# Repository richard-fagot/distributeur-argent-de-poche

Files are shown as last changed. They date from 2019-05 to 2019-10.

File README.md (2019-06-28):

# Distributeur automatique d'argent de poche pour les enfants.

Pour qu'ils puissent faire "comme les grands", avoir une carte bleue personnalisée et saisir un code pour pouvoir retirer leur argent de poche au distributeur, mais uniquement le samedi.

L'objectif est de faire un truc fun pour les enfants (et pour moi aussi du coup :D). Et comme tout ne va pas se dérouler sans accros, j'en profite pour tenir un journal de bord des problèmes rencontrés et des solutions trouvées pour les résoudre.

Tant qu'à y être, ça me semble intéressant de partager tout ça, alors ce journal de bord sert de base à une présentation sous forme de quickie plein de trucs et astuces dans chacun des domaines du projet.

# Disciplines associées

- **La programmation Arduino**, pour coder la logique du distributeur :
    - C++,
    - Optimisation de la taille du code généré,
    - Minimisation de la fragmentation du tas,
    - Gestion du temps ;

- **L'électronique**, pour l'alimentation, les différents composants autour de l'arduino, la fabrication du PCB, la lecture de carte à puce... :
  - Design du schéma életronique,
  - Routing,
  - Gravure du PCB,
  - Soudage ;

- **La conception 3D** pour dessiner les pièces mécaniques, supports et boitier du distributeur :
    - Conception des pièces,
    - Définition des liaisons mécaniques,
    - Assemblage des différents éléments entre eux ;

- **L'impression 3D**, pour fabriquer les pièces conçues sur mesure :
    - Slicing,
    - Prise en compte des contraintes liées au FDM ;

# Matériel
- Arduino Nano ;
- Pavé numérique à matrice (keypad) ;
- Écran LCD 2004 (4 lignes de 20 caractères) avec module I2C ;
- Module RTC DS3231 (ne pas prendre le DS1307 car il dérive beaucoup (il peut perdre plus d'une minute par jour)) en I2C ;
- 2 micro servos type HXT900 ;
- Connecteur carte à puce ;
- Lot de carte à puce vierge SLE4442.

# Logiciel
- [**Arduino IDE**](https://www.arduino.cc/en/Main/Software) ou VSCode avec l'extension Arduino ;
- [**Fusion 360**](https://www.autodesk.com/products/fusion-360) pour modéliser les pièces mécaniques ;
- [**Cura**](https://ultimaker.com/en/products/ultimaker-cura-software) pour préparer les pièces destinées à l'impression 3D ;
- [**Tinkercad**](https://www.tinkercad.com) pour la simulation d'un environnement Arduino ;
- [**EasyEDA**](https://easyeda.com) pour la conception de la partie électronique et du routage du PCB.

# Références
- Éviter la fragmentation de la pile : https://cpp4arduino.com/2018/11/06/what-is-heap-fragmentation.html 
- SLE4442 sur hackaday: https://hackaday.com/2008/11/25/how-to-read-a-fedex-kinkos-smart-card-sle4442/
- SLE4442 datacheet : http://www.smartcardsupply.com/PDF/DS_sle4432_42_0795.pdf
- SLE4442 sur docplayer : https://docplayer.fr/3533459-Carte-a-puce-sle-4432.html
- SLE4442 Librairie de lecture/écriture pour arduino : https://sourceforge.net/p/arduinosclib/wiki/Home/
- LCD 2004 https://www.gotronic.fr/pj2-sbc-lcd20x4-fr-1440.pdf
- D13 en input et pullup ne marche pas : https://www.developpez.net/forums/d1623869/general-developpement/programmation-systeme/embarque/arduino/propos-led_builtin-arduino-nano/

# Changement de taille programme

Passage de 61% à 57%
1. sans optim 18740
1. string name -> char name[21] 18674
1. dans un case string -> char 18596
1. un sprintf explose la taille 19246
1. remplacé par {'0'+total} 17740
1. sort la condition du if -> 17728

Plus tard
1. Aprés la création de la classe SamrtCard 12620/1046
1. MyKeyPad                                 12700/1070
1. Suppresion des Serial                    11522/821 (ce sont les string à la volée qui occupent la mémoire dynamique)
1. MyTime                                   11522/821

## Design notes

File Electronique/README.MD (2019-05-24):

Schéma électronique créé avec [EasyEDA](https://easyeda.com)

Le fichier DAAP.json est un export direct d'*EasyEDA*.

Les PDF sont les exports imprimables du schéma et du PCB.

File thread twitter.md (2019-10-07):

#

Un petit #THREAD pour détailler un peu plus mon talk au #DevfestToulouse
⬇️⬇️⬇️

#

Ce projet fait intervenir plein de domaines différents : conception 3D, impression 3D, électronique, arduino, C++, fabrication de PCB, un peu de mécanique, etc.

#

La conception 3D a été faite avec #Fusion360 (mais on peut utiliser #sketchup #Blender3d et plein d'autres) parce que c'était nouveau pour moi, il est super intuitif et qu'il y a une grosse communauté autour de ce logiciel pour apprendre facilement à s'en servir.

==> photo du projet fini dans Fusion360

#

Le design a été pensé pour tenir compte des contraintes de l'#impression3D :
- limiter les porte-à-faux ;
- tenir compte du sens d'impression des pièces subissant des contraintes mécaniques ;
- limiter la quantité de matière ;
- Faire des pièces qui s'impriment en 2h à 3h max.

#

J'ai voulu des temps d'impression courts d'une part parce que j'ai régulièrement des coupures de courant chez moi et que mon imprimante n'a pas de fonction "resume" et, d'autre part, parce que ça facilite le prototypage en pouvant plus facilement refaire une pièce défectueuse.

#

Pour la partie électronique j'ai utilisé ces composants :
- écran LCD2004 (20 cols, 4l) ;
- module I2C pour le LCD ;
- module RTC (horloge temps réel) ;
- Arduino nano ;
- Clavier matriciel 4x4 ;
- Servo HXT900 de modélisme ;
- Connecteur de carte à puce ;
- Carte à puce SLE4442.

#

Tous ces composants ont une librairie qu'on trouve facilement dans le gestionnaire de bibliothèque sauf pour la carte à puce. Il faut aller la trouver sur le net : https://sourceforge.net/p/arduinosclib/wiki/Home/
Et se la garder quelque part au cas où le lien disparaisse.

#

D'ailleurs, je vous recommande d'annoter vos imports de librairie dans le code avec suffisamment de détails pour la retrouver. Les librairies pour clavier matriciel ont la fâcheuse tendance à s'appeler "keypad.h".

#

Pour programmer la carte à puce et y mettre le code secret, la somme d'argent à distribuer et le prénom de l'enfant c'est par là : https://github.com/richard-fagot/DAAP-Smartcard

#

Sans rien changer aux branchements du distributeur on peut l'utiliser tel quel pour programmer une carte à puce, le mettre à l'heure et faire la distribution d'argent de poche uniquement en téléversant le programme qui va bien.

#

Pour la carte à puce : https://github.com/richard-fagot/DAAP-Smartcard

Pour l'heure il suffit de prendre les programmes d'exemple du DS3231.

#

L'horloge me permet de contrôler que les enfants ne font pas plus d'un retrait par semaine (samedi ou dimanche) en gérant les changements de mois et les années bissextiles.

#

Je n'en ai pas parlé pendant le talk mais il y a du code #cpp, beaucoup de code, que vous pouvez retrouver là : https://github.com/richard-fagot/distributeur-argent-de-poche/tree/master/sketch

Le point d'entrée c'est Sketch.ino à ouvrir dans l'IDE arduino : https://www.arduino.cc/en/Main/Software

#

Dans ce sketch il y a une première fonction 𝘀𝗲𝘁𝘂𝗽() d'initialisation des paramètres du programme et des périphériques. Le fonction 𝗹𝗼𝗼𝗽() contient la logique du programme. Une bonne pratique consiste à faire en sorte qu'elle s'exécute très rapidement.

#

C'est surtout pour dire qu'il faut remplacer les 𝗱𝗲𝗹𝗮𝘆() qui bloquent l'arduino par :

	𝗶𝗳(𝗺𝗶𝗹𝗹𝗶𝘀() - 𝗽𝗿𝗲𝘃𝗶𝗼𝘂𝘀𝗠𝗶𝗹𝗹𝗶𝘀 > 𝗺𝗼𝗻𝗗𝗲𝗹𝗮𝘆) {...}

ça permet de faire d'autres tâches en attendant qu'un servomoteur ait fini de tourner par exemple.

#

La gestion du temps c'est compliqué ! Sur ce projet j'ai mis en place une machine à état parce que c'est ce qui me semblait le plus naturel pour gérer les différents états du distributeur mais aussi les délais et notamment ceux qui concernent les mouvements des servos.

#

Mais attention aux noeuds au cerveau :D

#

Pour coder on peut utiliser l'IDE Arduino mais on peut aussi utiliser VS Code avec l'extension #Arduino (il sert à tout ce VS Code) et ça marche plutôt bien même si il y a des écarts sur la taille des programmes. Il faudrait regarder du côté des options de compilation du #cpp.

#

À un moment j'ai grillé un servo en faisant une fausse manipulation. J'ai cherché un logiciel qui permettrait de simuler un environnement #arduino et des périphériques autours, comme des servos.

#

Hé bien ça existe ! c'est @tinkercad. J'ai fait une grosse partie de la conception grâce à ça, sans rien casser ! On peut s'en servir comme dans @scratch ou en code pur. Et utiliser des servos, des LCD, la mémoire EEPROM...

#

Quand la phase de prototypage est terminée on va créer le PCB. J'ai utilisé @EasyEDA mais on peut utiliser aussi @kicad_pcb qui est open source.

==> image du pcb

#

Après il suffit de suivre cet excellent tuto de @Heliox_Lab en prenant un papier glacé le plus fin possible pour éviter le gondolage : https://youtu.be/UTe3eYCj6vU

#

Et quand tout est enfin terminé, on profite du résultat final :

(Qu'est-ce que t'en dit @Heliox_Lab ? :D)

Si vous avez des questions, mes DM sont ouverts.

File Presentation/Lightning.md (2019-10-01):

---
pagetitle: DAAP
lang: fr-FR
compile: pandoc -t revealjs -V theme=white -s Lightning.md -o lightning.html --css=devfest.css 
---

# Distributeur Automatique d'Argent de Poche

Richard Fagot

:::notes

1. Tiens-toi bien ;
1. Pense à ta première phrase ;
1. Prend une inspiration ;
1. Embrasse la salle d'un regard et lance-toi.

==> Bonjour à tous et bienvenu. Il y a quelques temps avec mon épouse...
:::

# {data-background-image="assets/img/calvin.png" data-background-size="contain"}
<!--![](assets/img/calvin.png)-->

::: notes
Passer rapidement.

==> Mais on ne s'est pas lancé comme ça...
:::

# 
:::notes
On trouve des règles qu'on a choisi d'appliquer. 

- règles de l'argent de poche :
  - quantité libre,
  - distribution 1x/sem,
  - Pas de privation,
  - not(rémunération),
  - l'enfant dépense librement.

==> L'idée étant qu'ils puissent faire comme les grands...
:::

# {data-background-image="assets/img/comme-les-grands.jpg"}

::: notes

==> quitte à faire comme les grands, est-ce qu'on ne pourrait pas aller plus loin ?

:::

# {data-background-image="assets/img/fond-mouvement.png"}
<!-- image du servomoteur {data-background-color="#FDFAFE"}-->
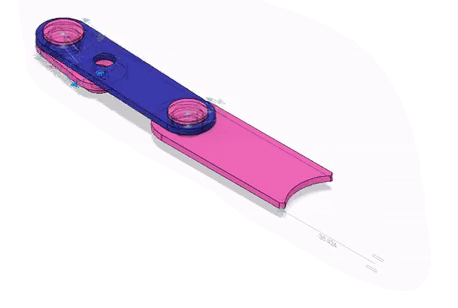
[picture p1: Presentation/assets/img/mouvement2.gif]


:::notes

Passez rapidement pour ne pas perdre l'attention de l'auditoire.

Transforme mvt de rotation en translation alternatif

==> Il y a une colonne de pièce, on pousse celle du dessous...
:::

# 
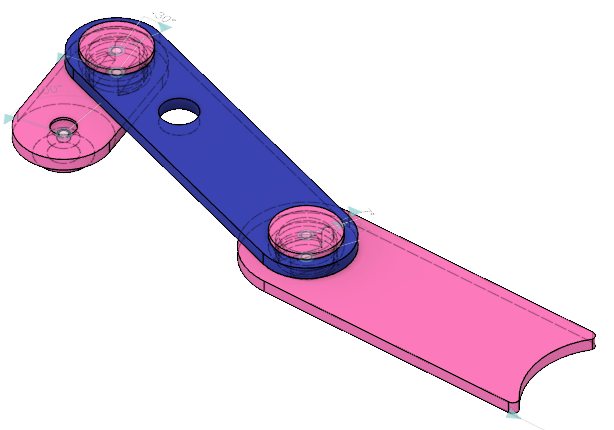
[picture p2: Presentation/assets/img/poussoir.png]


::: notes
  - sujet en soi ;
  - explication des différentes pièces ;
  - penser à la méthode de production.

  ==> vous pourrez venir me voi à l'office hour pour savoir pourquoi il y a un trou dans la bielle.
:::

# {data-background-image="assets/img/impressionPosition.png"}
<!--
![](assets/img/Impression clip.png){ width=1000px }
-->
:::notes
  => pour maintenir tout ça en place il faut un support.
:::

# 
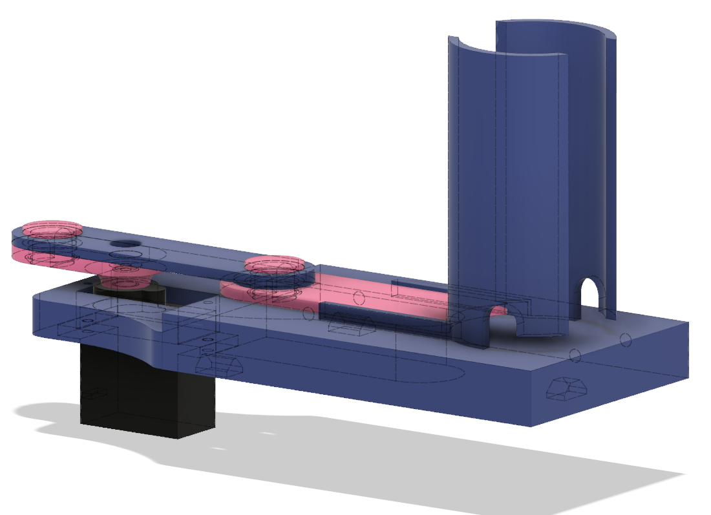
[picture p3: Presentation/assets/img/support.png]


::: notes
  => on peut distribuer, oui, mais combien ? il faut stocker la somme quelque part.
:::

# 
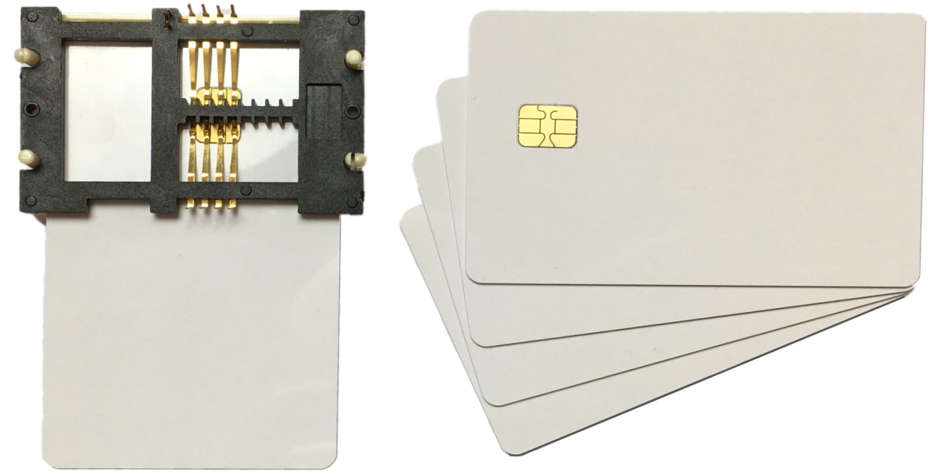
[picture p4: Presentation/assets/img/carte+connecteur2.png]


:::notes
  ne pas parler de la secu.
  - ~~carte sécurisée~~ ;
  - connecteur ;
  - on y stocke : code, prénom et somme.

  => il faut interagir avec l'utilisateur.
:::

# 
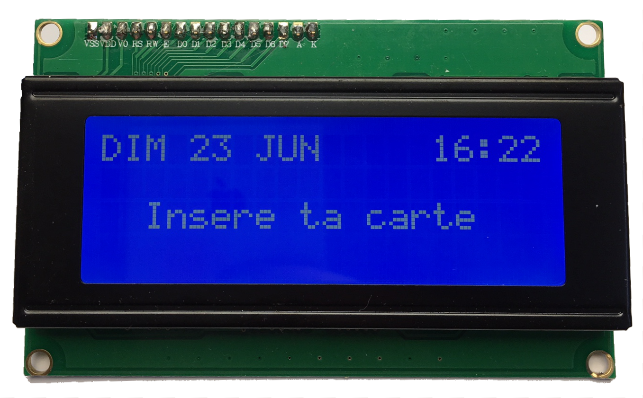
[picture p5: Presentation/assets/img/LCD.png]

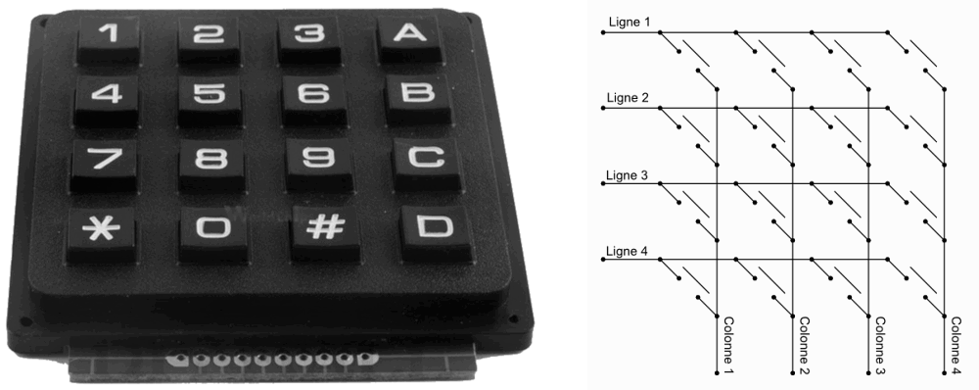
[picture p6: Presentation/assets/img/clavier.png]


::: notes
  ==> Il faut contrôler tout ça.
:::

# 
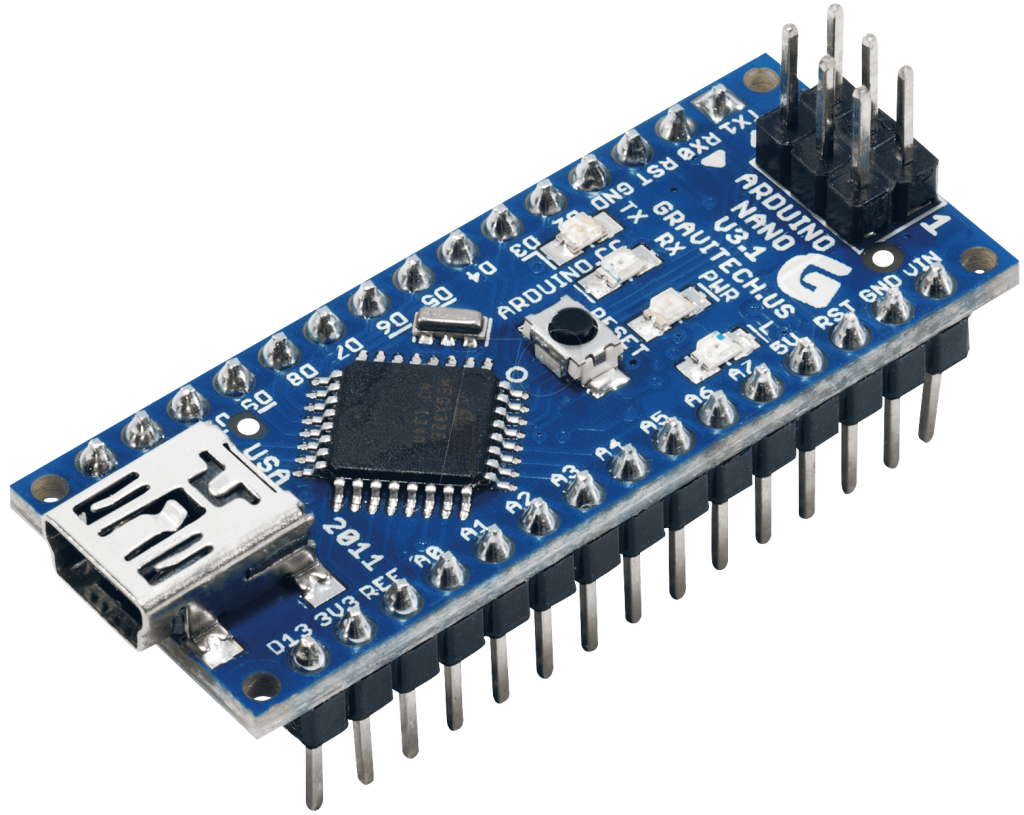
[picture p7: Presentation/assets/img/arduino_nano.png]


:::notes
  - peu de broches => I2C ;
  - Retour aux bases de l'info : pointeurs, références, gestion de la mémoire (fragmentation).

  ==> Tous ces éléments il faut les connecter pendant le prototypage.
:::

# {data-background-image="assets/img/prototype.jpg"}
<!--![](assets/img/prototype.jpg){ height=1080px }
![](assets/img/breadboard.jpg){ height=600px }-->

::: notes

  ==> Ce n'est pas utilisable pour le produit final, il faut un PCB.
:::

# {data-background-image="assets/img/circuit.png" data-background-size="90%"}
<!--![](assets/img/circuit.png){ height=650px }-->

::: notes
  - fait avec EasyEDA ;
  - Pas de fils de connection, mais des étiquettes qui permettent de tout ordonner par fonction.

  ==> Cette description logique permet de passer au routage.
:::

# {data-background-image="assets/img/routing_Bleu.png" data-background-size="60%"}
<!--![](assets/img/routing_Bleu.png){ height=700px }-->
<!--![](assets/img/PCB2.png){ height=600px }-->

::: notes
  - automatique ne marche pas trop ;
  - on fait des aller-retour avec le schéma électronique pour affiner le routage.

  ==> ensuite on imprime et après un peu de chimie et avoir piqué le gemey-maybelline de ma chère moitié.
:::

# {data-background-image="assets/img/dissolvant.jpg" data-background-size="50%"}
<!--![](assets/img/dissolvant.jpg){height="700px"}-->

::: notes
comment ne pas perturber avec le solvant.

  ==> c'est bien le flacon rose qu'il faut, on obtient ça.
:::

# {data-background-image="assets/img/PCB étamé.jpg" data-background-size="60%"}
<!--![](assets/img/PCB étamé.jpg){ width=800px }-->

::: notes
  ==> après perçage et soudage on obtient un résultat bien plus propre que le tas de nouille.
:::

# {data-background-image="assets/img/circuit-monté.jpg" data-background-size="100%"}
<!--![](assets/img/Circuit imprimé.jpg){ width=700px }-->

::: notes
  ==> Tout ça c'est beau mais il faudrait un beau boitier pour ranger le tout.
  ==> Et après de nombreux tests.
:::

# {data-background-image="assets/img/tests.png"}

# 
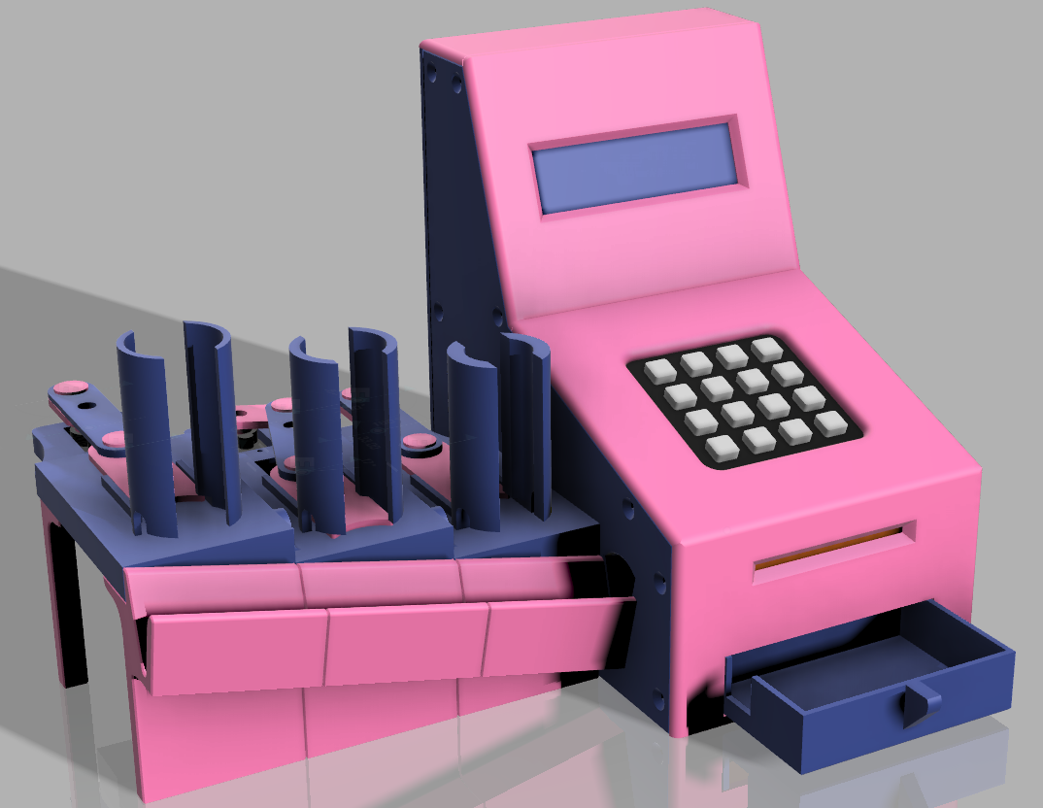
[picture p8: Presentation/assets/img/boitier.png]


# 
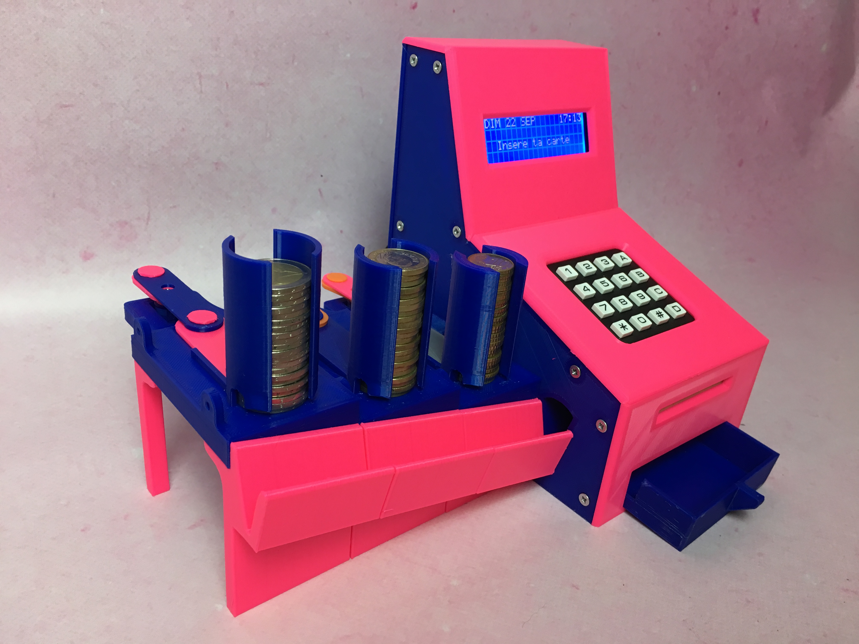
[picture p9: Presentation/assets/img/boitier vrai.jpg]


# Démo


# 

* 2 mois de travail++ ;
* Mécanique, Conception/Impression 3D, Électronique, Arduino, PCB, soudure... ;

# Office Hour

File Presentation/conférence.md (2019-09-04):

---
pagetitle: DAAP Conf
lang: fr-FR
---

<!-- Phrase d'introduction -->
# Distributeur Automatique d'Argent de Poche

Richard Fagot

:::notes
1. Tiens-toi bien ;
1. Pense à ta première phrase ;
1. Prend une inspiration ;
1. Embrasse la salle d'un regard et lance-toi.
:::

<!-- Pause blagounette -->
# 
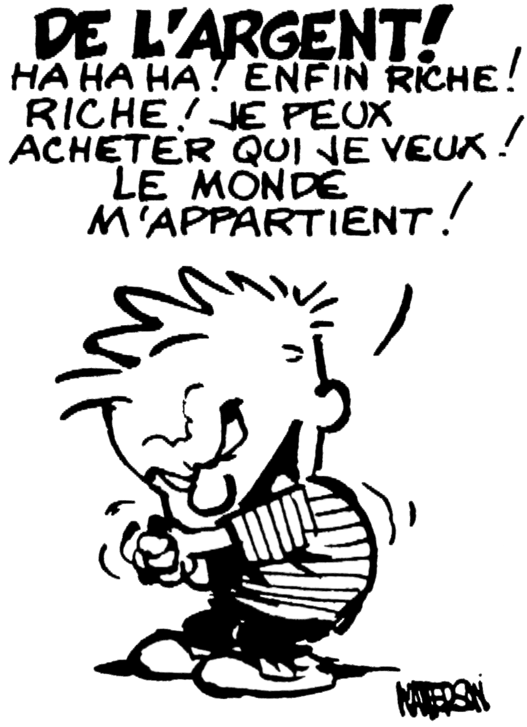
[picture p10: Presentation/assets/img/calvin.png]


::: notes
Passer rapidement.

==> littérature sur le sujet
:::

<!-- Courte introduction à l'argent de poche et genèse du projet -->
#

:::notes
- règles de l'argent de poche (qté libre, 1x/sem, Chq sem, not(rémunération), libre).

==> quitte à faire comme les grands, est-ce qu'on peu aller plus loin ?
:::

<!-- Le poussoir -->
# 


::: notes
**Le poussoir**

- mouvement bielle-manivelle ;
- rotation -> translation.

==> parce que j'aime bien le mouvement
:::

#
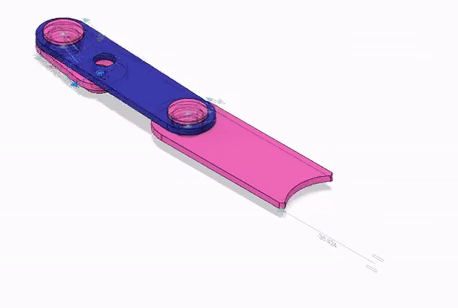
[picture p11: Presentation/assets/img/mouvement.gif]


:::notes
Passez rapidement pour ne pas perdre l'attention de l'auditoire.

- joli ;
- hypnotique ;
- facile à concevoir.

==> il est constitué de != éléments
:::

# 


:::notes
**Le poussoir**

- description + servo ;
- conception dans fusion360 ;
- axes qui maintiennent les pièces ensembles lego.

==> essai paramètre fexibilité, jeu, je suis arrivé à ça.
:::

<!-- Clip -->
#
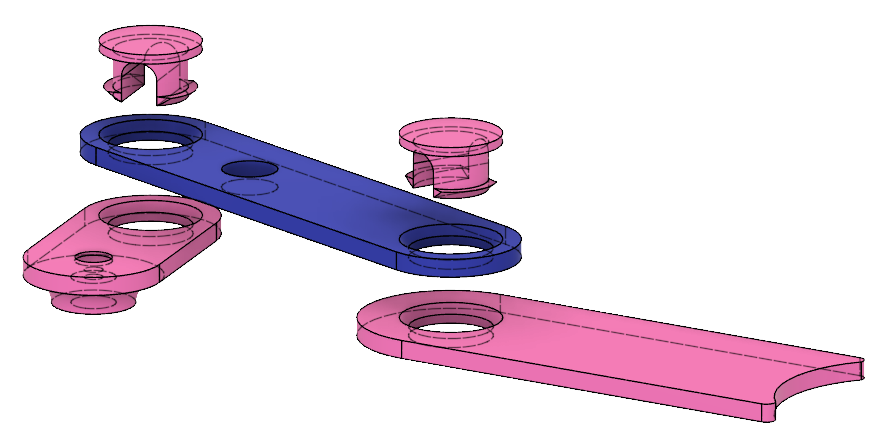
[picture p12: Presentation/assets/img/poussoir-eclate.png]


:::notes
- Description du clip ;
- Pièce complexe : penser à l'impression 3D
:::

#
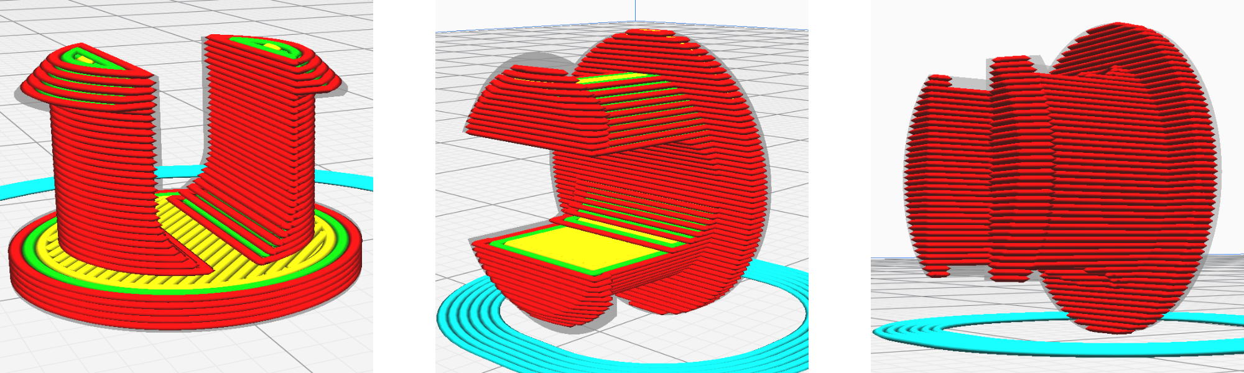
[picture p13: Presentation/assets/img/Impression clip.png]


:::notes
  - paramètres d'impression dans Cura (Simplify3D) ;
  - Pros'n Cons des 3 impressions ;
  - insertion manivelle/poussoir ;
  - mouvement rectiligne, support servo, réservoir pièce.

  ==> Je vous présente le support.
:::

<!-- Le support -->
#
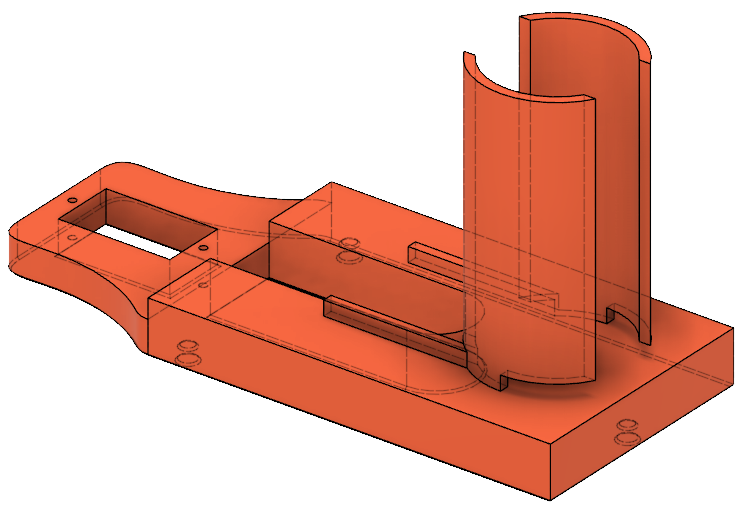
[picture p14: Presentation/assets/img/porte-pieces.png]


::: notes
  - support servo ;
  - guide poussoir ;
  - Diamètre réservoir
  - ouverture réservoir ;
  - rainure réservoir.
git
  ==> système complet, y' plus qu'à le commander
:::

<!-- Arduino -->
#


:::notes
  - Facile à programmer, communauté ;
  - compact ;
  - HE14 à un rang ;
  - nombre de broches ;
  - µC quesako ?

==> Code librairie **OU** chaque carte a son schéma d'entrée-sortie
  
:::

##
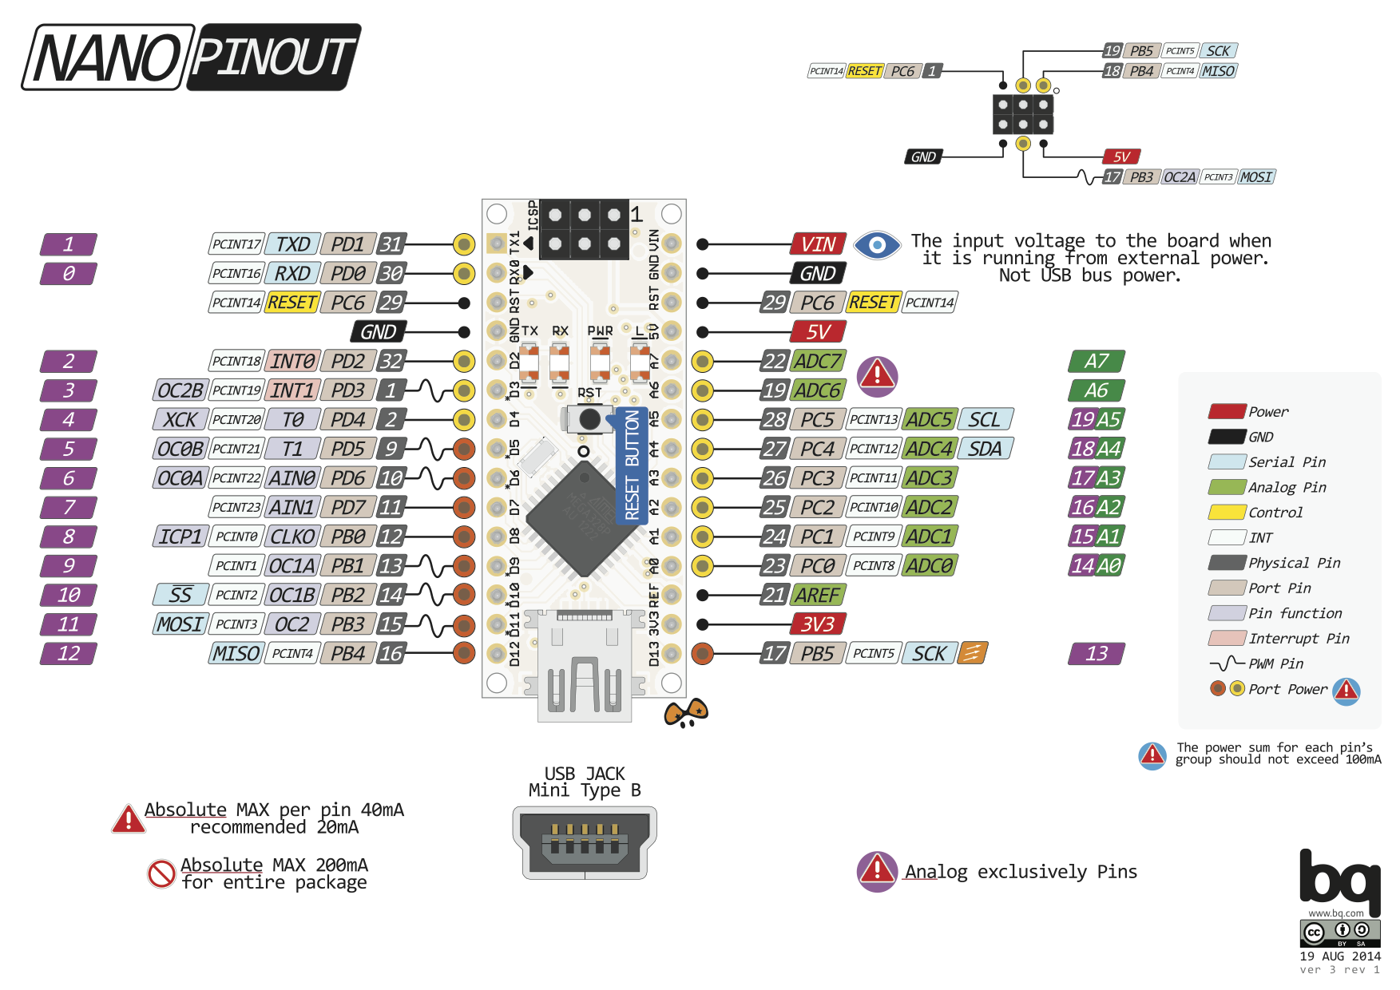
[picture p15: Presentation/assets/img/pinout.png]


:::notes
- détail des broches (22 nano).

==> arduino fourni pleins de librairies : servo (PWM? ou code?)
:::

<!-- PWM -->
## PWM
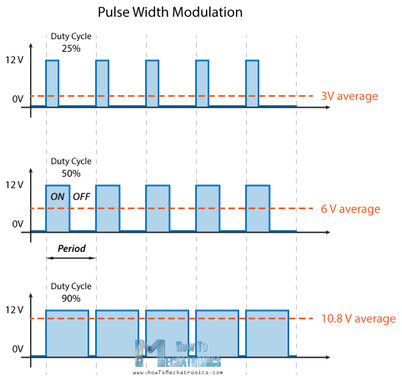
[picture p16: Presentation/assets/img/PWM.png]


:::notes
  - rapport cyclique pour générer signaux pseudo-analogiques ;
  - Pulse Width Modulation
  ==> en terme d'api c'est très facile à utiliser
:::

<!-- Contrôler le servo -->
#
```c++
#include <Servo.h>

Servo myServo;
byte position;
byte servoPin;

void setup() {
    myServo.attach(servoPin);
    myServo.write(position);
    delay(1000);
    myServo.detach();
}

void loop() {...}
```

::: notes
==> système de distribution, combien à distribuer ?
:::

<!-- Séquenceur 
## 
```cpp
CoinPusher *coinPushers[MAX_PUSHER_COUNT];
CoinPusher *sequence[MAX_SEQUENCE_COUNT];

while(remaining != 0) {
  int actualCoinValue = 
     coinPushers[pusherIndex]->getFacialValue();
  byte pushCount = remaining / actualFacialValue;
  for(int i = 0 ; i < pushCount ; i++) {
      sequence[sequenceIndex] = coinPushers[pusherIndex];
      sequenceIndex++;
  }
  remaining -= actualFacialValue * pushCount;
}
```
-->

<!-- Stockage quantité -->
#
:::notes
  - dans le code :
    - pas sexy,
    - flasher arduino si changement ;
  - dans une mémoire extérieure : la carte à puce
:::

<!-- SLE 4442 -->
# SLE 4442
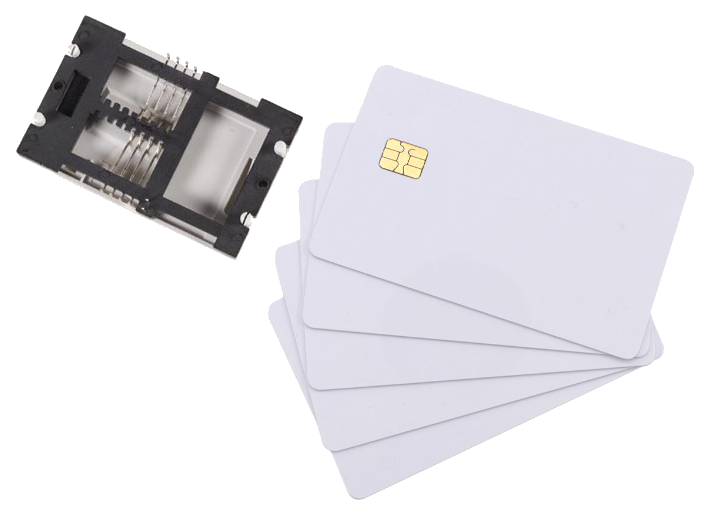
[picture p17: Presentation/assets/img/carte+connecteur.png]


:::notes
  - carte sécurisée ;
  - connecteur ;
==> on y stocke
:::

<!-- Structure carte -->
# 
```cpp
struct {
  char name[20+1];
  int pocketMoney;
  int secret;

  byte nameLength;
};
```

:::notes
  ==> ça a l'air facile comme ça mais lib dure à trouver.
:::

<!-- Discours trouver la librairie SClib-->
# 

:::notes
  - faillit abandonner
==> lib implémente SLE4442, par exemple
:::

<!-- Protocole SLE4442 -->
#
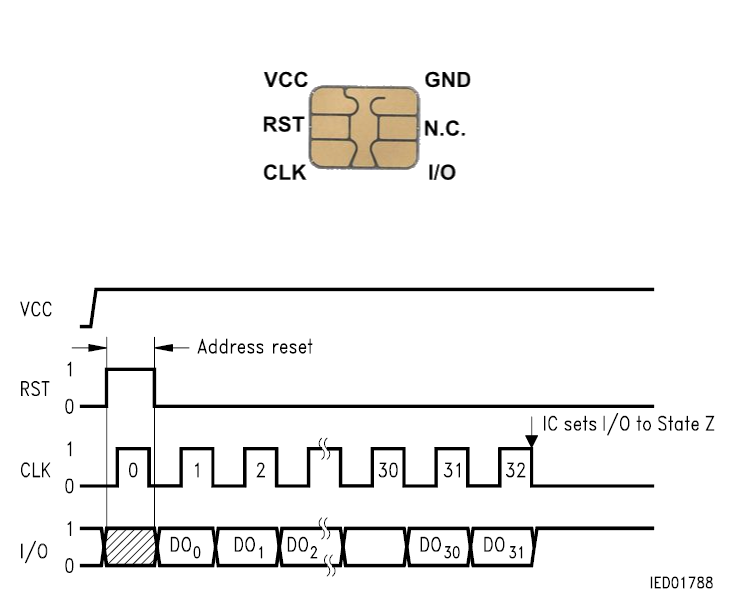
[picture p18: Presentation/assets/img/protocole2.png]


:::notes
- similaire aux télécartes (les aquariums dans lesquels on s'enfermait pour appeler avec un téléphone avec un gros fil relié à une boite obscure) ;
==> c'est ce qu'il se passe quand l'enfant insère la carte dans la machine, qui, par ailleur l'y invitait via LCD.
:::

<!-- Présentation de L'écran LCD -->
#


:::notes
  - 20x4
  - plein de lib
  - mais 6 broches
==> toujours chercher un peu pour diminuer le nombre de broches, I2C très répandu gros standard industriel grosse quantité d'équipements et par défaut dans arduino+pattes SDA/SCL
:::

<!-- Introduction au protocole I2C -->
#
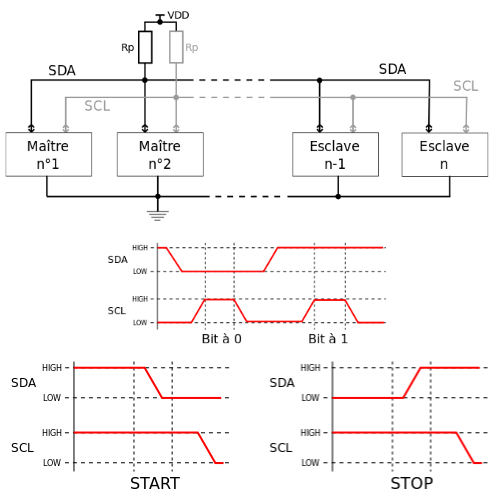
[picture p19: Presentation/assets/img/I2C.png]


:::notes
==> implémenté dans la lib Wire.h qui est utilisée dans la lib de l'écran qui est aussi simple d'utilisation.
:::

<!-- Librairie LCD -->
#
```cpp
#include <LiquidCrystal_PCF8574.h> // by Mathias Hertel

LiquidCrystal_PCF8574 lcd = LiquidCrystal_PCF8574(0x27);

lcd.setCursor(col, row);
lcd.print(message);
```
:::notes
==> fonctions utilitaire, effacer pour afficher d'autres messages comme demander de saisir le code.
:::

<!-- Clavier matriciel -->
#


:::notes
  - clavier 4x4 rigide ;
  - principe de fonctionnement ;
  - 8 broches !!!!! I2C possible mais faut le faire soi-même.
==> On a un système qui commence à être pas mal, mais il y a une règle : 1 fois par semaine.
:::

<!-- anti-rebond 
#
![](assets/img/rebond.png){height="400px"}

:::note
:::

#
![](assets/img/anti-rebond.png){height="400px"}

:::note
:::

-->

<!-- RTC -->
#
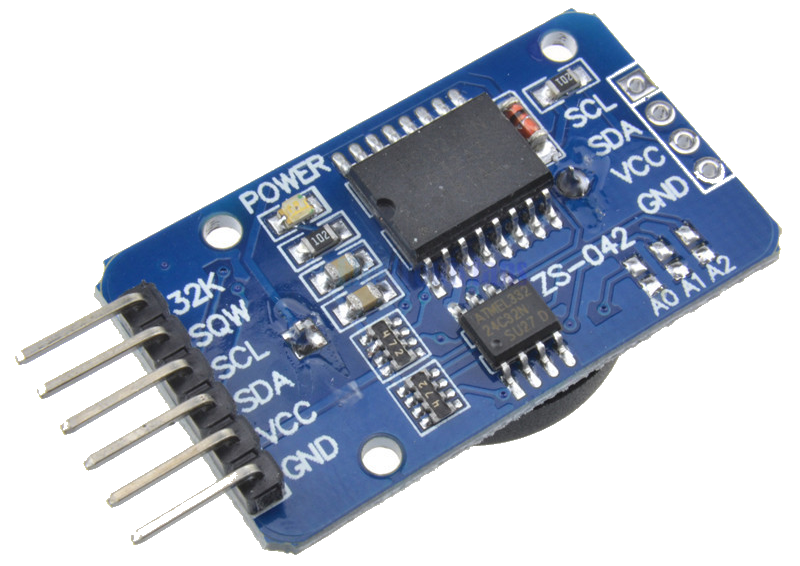
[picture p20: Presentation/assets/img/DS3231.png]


:::notes
  - horloge temps réél (DS3231)
  - getMillis() 50J (u_long 32 bit)
  - très peu de dérive (voire pas), temperature
  - DS1307 +1s/jour
:::

#
```cpp
#include <ds3231.h> //ds3231FS by Petre Rodan
ts timeDetails;

DS3231_get(&timeDetails);

timeDetails.wday;
```

:::notes
  - mise à l'heure se fait avec un des programmes d'exemple ;
  - système plutôt complet.

==> mais... (my little hacker) il va être mis entre les de hackers en herbe.
:::

# My Little Hackers
:::notes
- ... filous, il va être mis entre les de hackers en herbe ;
- certain qu'il vont tenter de hacker le système ;
- en fonction de la dernière date de retrait (années bisextile div/4 not(100) OU div/400)
- il faut retenir la date et pour ça y'a l'EEPROM.

==> j'ai confiance mais c'est une occasion de programmer l'EEPROM de l'arduino.
:::

<!-- EEPROM -->
#
```cpp
#include <EEPROM.h>

EEPROM.write(address, childCount);

struct DistributionDate lastDistributionDate;
EEPROM.get(address, lastDistributionDate);
```

:::notes
   
:::

<!-- Circuit électronique -->
#
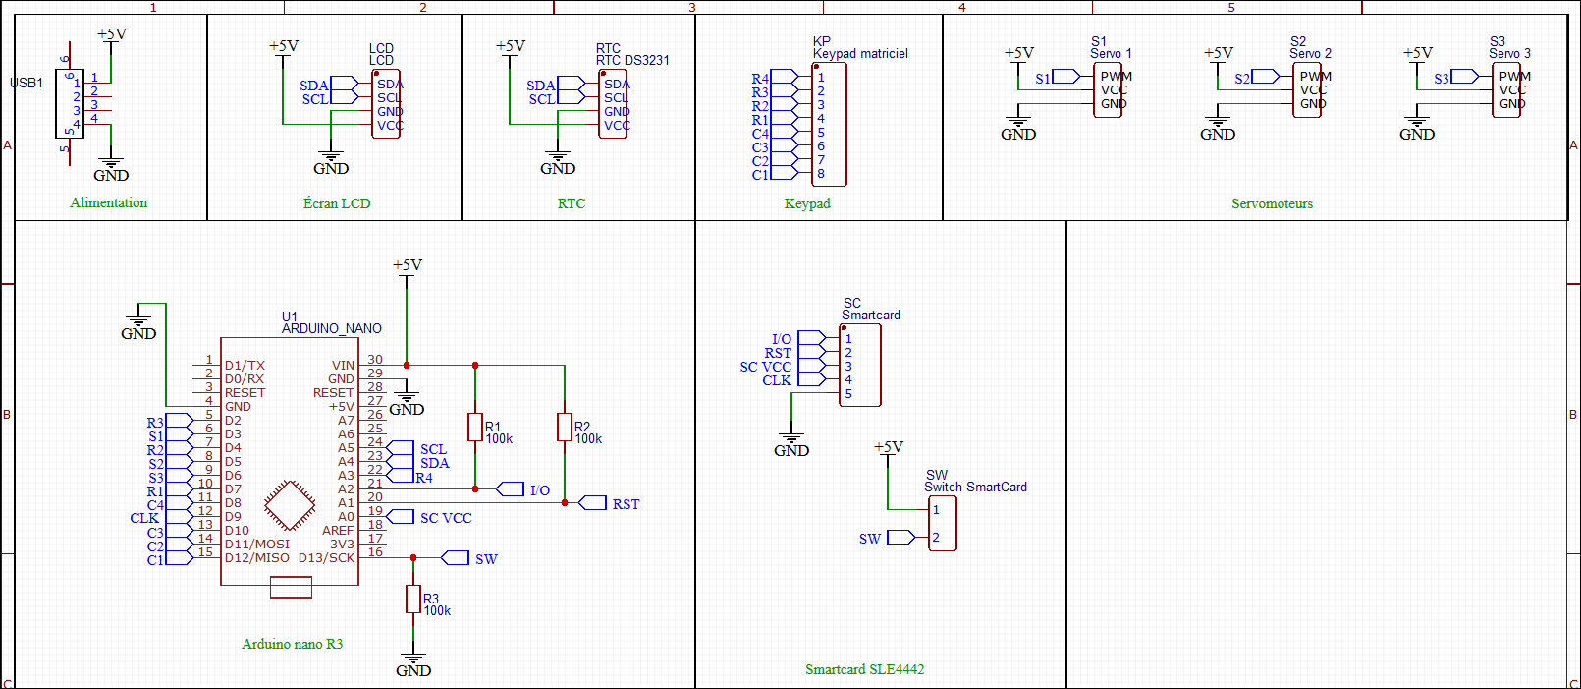
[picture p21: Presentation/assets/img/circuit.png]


<!-- PCB -->
#
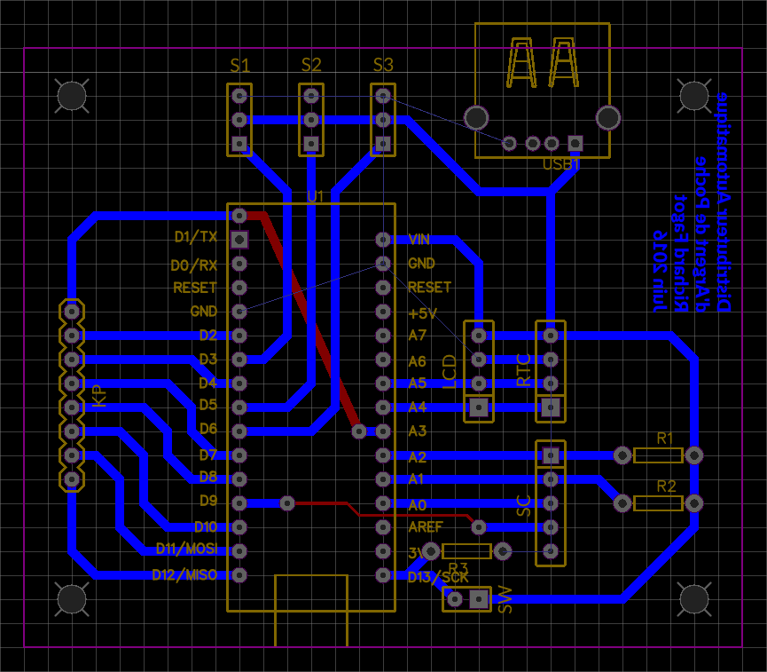
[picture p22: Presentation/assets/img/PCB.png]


#
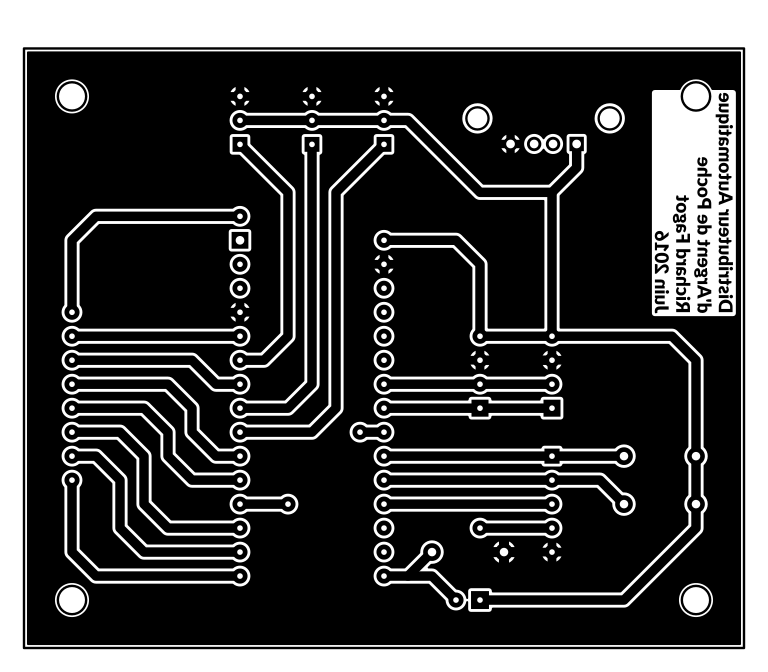
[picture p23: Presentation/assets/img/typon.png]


:::notes
Démo time ? 

**OU**

Fabrication ?

:::

<!-- Fabication -->
## Fabrication
  - Un prospectus en papier glacé ;
  - Une imprimante laser ;
  - Un marqueur indélébile ;
  - Perchlorure de fer ;
  - Étain chimique à froid ;
  - Récipents en verre ou plastique ;
  - et...

##
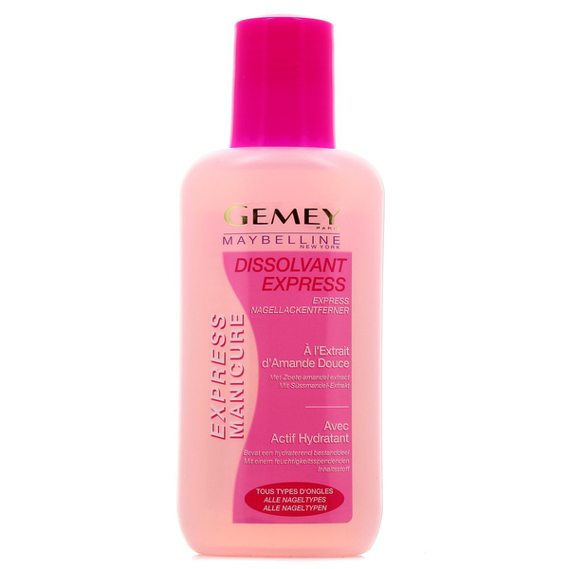
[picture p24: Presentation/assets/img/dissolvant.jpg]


# DEMO TIME
:::notes
Aujourd'hui, je suis plutôt satisfait du résultat et mes enfants adorent venir y retirer leur argent de poche.
:::

# Améliorations
  - Bug à corriger ;
  - Fabriquer le boitier ;
  - Menu (éditer une carte, heure, conf.) ;
  - Remplacer les distributeurs par des robots.

# Questions ?
  - Quels thèmes (pas) intéressants ? ;
  - Optimisation code arduino ;
  - Démo des logiciels ?
  - Plus d'astuces ;
  - ...

# Quelques liens

  - [Github du projet](https://github.com/richard-fagot/distributeur-argent-de-poche)
  - [Design de connections en 3D](https://www.3dhubs.com/knowledge-base/how-design-snap-fit-joints-3d-printing)
  - [Keypad I2C](https://playground.arduino.cc/Main/I2CPortExpanderAndKeypads/)
  - [Fusion 360](https://www.autodesk.com/products/fusion-360/free-trial)
  - [Cura](https://ultimaker.com/software/ultimaker-cura)
  - [EasyEDA](https://easyeda.com/)
  - [Tinkercad](https://www.tinkercad.com/)

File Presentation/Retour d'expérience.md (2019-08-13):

# Distributeur automatique d'argent de poche - Retour d'expérience

## Description du projet

## Domaines qu'il a fait intervenir
- **Design 3D** pour la conception des éléments mécaniques et boîtes ;
- **Impression 3D** pour la fabrication des éléments mécaniques et boîtes ;
- **Programmation Arduino** pour le développement de la logique du système ;
- **Electronique** pour les éléments autour de l'arduino ;
- **Cartes à puce sécurisées** pour stocker les informations nécessaires sur l'argent de poche à distribuer.

## Design 3D
Pour le design 3D j'utilise Fusion 360. ça marche bien et on peut même simuler les mouvements mécaniques.

C'est probablement la partie la plus longue car il faut beaucoup expérimenter, imprimer un draft pour voir ce que cela donne, adapter le design, etc.

Il faut toujours garder à l'esprit le mode de production des pièces, ici par FDM (Fused Deposition Modeling). Les pièces produites par cette méthode sont fragiles dans le sens de la hauteur. Des porte-à-faux peuvent apparaître, certains nécessitant des supports pour le pas voir ces parties s'affaisser à l'impression.

### Comment visser le système bielle-manivelle
Au repos et à l'initialisation du distributeur, toutes les bielles-manivelles sont en retrait. Dans cette position la manivelle est totalement cachée sous la bielle et la vis de fixation sur le servo n'est pas accessible. Au début je fixais la manivelle sans insérer le système dans le rail et je jouais sur la flexibilité du plastique pour la rentrer de force.

Et puis une petite ouverture de 5mm pratiquée dans la bielle, là où se trouve la vis dans la position de repos, c'est bien plus pratique.

### tenir compte de la variabilité de la taille des pièces
Après avoir grillé un servo j'ai du en acheter d'autres. Il se trouve que la visserie n'était pas identique, notamment au niveau du maintient de l'axe : la vis avait une tête plus large et plus haute qui ne rentrait plus dans l'espace aménagé dans la manivelle.

Penser à cette variabilité lors de la conception des pièces. Heureusement, en utilisant les bons points de repère dans les sketch ça a été facile de corriger.

### Eviter les pattes d'éléphant
Au début de l'impression, les premières couches sont un peu plus écrasé sur la base ce qui fait qu'elles sont un peu plus large que par la suite.
Pour minimiser le phénomène il faut faire la partie de la pièce qui sera en contact avec le plateau un peu plus étroite en pratiquant un chanfrein par exemple (de 0.6 ou 0.8). Dans tous les cas, si il doit y avoir un assemblage au niveau de ces endroits il y a peu de chance d'avoir un raccord aussi parfait qu'en haut d'une pièce.

### Platines d'assemblage du connecteur de carte à puce
La conception de ces éléments en forme de haricot s'est déroulée en plusieurs étapes :

1. Modélisation du connecteur de carte à puce avec les éléments importants pour la conception des supports (emplacement des taquets, broche, encombrement général) ;
1. Design d'une platine rectangulaire plus grande que le connecteur sur laquelle on place avec précision les trous pour les taquets du connecteur et ceux pour les vis de maintient dans le boitier ;
1. On passe dans l'espace de travail *simulation*, en appliquant des *contraintes structurelles* à l'emplacement des vis et des charges orientées vers l'arrière sur les trous des taquets pour simuler l'insertion de la carte à puce. La résolution, en conservant 30% de matière environ (dépend de la surface du support initial), conduit à une forme en haricot sans lien entre les deux. Ici ce n'est pas génant, ajouter une liaison rigide entre les deux haricots n'apporte rien au niveau maintient en place ;
1. Retour dans l'espace modélisation pour concevoir les platines de maintient ;
1. La première impression permet de montrer que si les trous sont tous bien de la bonne taille, l'effet patte d'éléphant empêche le bon assemblage des éléments ;
1. Modification du design pour ajouter un chanfrein au niveau des trous au contact du plateau d'impression.

## Impression 3D
### Laisser les pièces refroidir
A la fin d'une impression les pièces sont encore chaudes. Si on tente de les décoller à ce moment là elles risque de se déformer irrémédiablement.

Il faut être patient en impression 3D, patienter pendant le looooooonnnnnng temps d'impression et patienter pendant le refroidissement des pièces.

## Programmation Arduino

### La gestion du temps sans Delay
Diantre que c'est compliqué.

### Tinkercad

Après avoir malencontreusement grillé une carte, j'ai cherché une solution qui permette de tester son code dans un environnement virtuel, et donc sans risques pour la carte le temps de la première mise au point.

Pour cela j'ai utilisé *Tinkercad* qui offre, entre autre, un environnement de simulation Arduino.

#### Avantages
- offre un environnement virtuel sans risque pour les cartes physiques ;
- permet de commencer à travailler sur du matériel qu'on n'a pas encore reçu (écran LCD, calvier...) ;
- exécute le code arduino (simulation, on peut voir les LED s'allumer, les servos tourner....) ;
- certaines librairies sont disponibles (Servo, Keypad...) ;
- simulation du serial ;
- possibilité de coder en *Scratch* ;
- En ligne, on peut reprendre son travail depuis n'importe quel ordinateur connecté à internet ;
- On peut copier-coller le code dans l'Aduino IDE et le téleverser, ça marche (modulo quelques ajustements de type délai d'attente pour que les servos aient fini leur action, debounce (pas de rebond des interrupteurs en virtuel...) ;
- Il y a des circuits tout fait, ce qui fait gagner du temps (design, code...), par exemple pour controler un LCD.

#### Inconvénient
- Seulement Arduino UNO R3 ;
- Bibliothèque composants limitée (pas d'I2C par exemple : obligé d'utiliser un autre arduino virtuel  pour simuler l'I2C) ;
- Bibliothèque de librairies limitée ;
- Impossible de faire appel à des librairies externes (choix interne limité) ;
- 3 arduinos, un lcd et clavier : tinkercad n'en demandait pas tant...

### Optimisation du code

#### Fragmentation du tas
Le diable s'habille en string :
https://hackingmajenkoblog.wordpress.com/2016/02/04/the-evils-of-arduino-strings/

https://cpp4arduino.com/2018/11/06/what-is-heap-fragmentation.html

Le fait de remplacer des `string` par des `char*` permet de gagner pas mal de place en mémoire (taille du programme après compilation)

| Taille | Action |
|---|---|
|8466| avec `display(String)` et `log(string)`|
|8068| avec des `char*`|

### Tenir compte des spécificités de chaque arduino
Tous les arduinos n'ont pas forcément le même comportement avec le même code :
 - les broches ne sont pas forcéments les mêmes ;
 - les fonctions associées au différentes broches peuvent être différentes (par exemple le timer1 qu'on trouve sur un uno se retrouve sur la broche 11 d'un mega) ;
 - la fonction Serial nécessite un `while(!Serial) {}` sur un leonardo. C'est spécifique aux cartes basées sur un AVR de type 32u4 dont la Leonardo fait partie (mail la yùn également).

## Électronique
### Le bruit des servomoteurs
Les servos que j'ai choisi sont commandés en PWM qui traduit l'angle auquel on veut que le servo aille.
Une fois arrivé à l'angle indiqué le servo fait tout ce qu'il peut pour s'y maintenir. Il fait des gros efforts pour ça et ça s'entend...
Le distributeur ayant vocation à se trouver dans le salon, c'était inenvisageable d'avoir ce bruit en permanence.
Comme je n'ai pas besoin que le servo maintienne sa position (par de contraintes extérieures pour modifier sa position), la première solution à laquelle j'ai pensé est de commander l'alimentation via l'arduino (alimenté pendant les mouvements, coupé le reste du temps). ça prend deux broches supplémentaires plus un peu d'électronique pour implémenter tout ça. Rien de méchant mais les broches sont précieuses, on en a peu.

En regardant plus attentivement la documentation j'ai découvert le ``Servo::detach()`` qui permet de "déconnecter" le servo de sa broche. 
> En plus, si on a utilisé les broches 9 et/ou 10 on peut les utiliser à nouveau pour faire du PWM ?????

### Alimentation de l'ensemble
Ce qui consomme le plus ici ce sont les servomoteurs.

| Composant | Consommation (mA) |
|---|:---:|
| Arduino Uno R3 | x |
| Servox2 | x |
| LCD | x |
| Clavier | x |
| RTC | x |

### Les parasites
Lorsqu'on fait les montages sur les breadboards on relie les différents éléments entre eux avec des fils. Et ces fils font de magnifiques antennes sensibles au 50Hz du courant domestique, aus lampes à décharge, aux moteurs qui tournent ou tout simplement quand on les touche (c'est même une propriété utilisée dans les capteurs capacitifs).

Et il arrive que le montage ait des comportements étranges : des actions lancées par un bouton sur lequel on n'a pas appuyé, un écran LCD qui se met à verser dans la magie noire en inscrivant des signes cabalistiques mystérieux...

Pour éviter cela, il faut ([ref](https://forum.arduino.cc/index.php?topic=78406.0)) :
 - charger les lignes, en mettant une résistance de pullup par exemple ;
 - ajouter un condensateur de filtrage entre la ligne et la masse pour bloquer les signaux basse fréquence.

### Conception du PCB
Il faut y aller par raffinements successifs : l'objectif est de placer les composants autour de l'arduino de telle sorte que les pistes ne se croisent pas. Déjà, en soit, ce routing n'a rien d'évident mais en plus on peut ne pas avoir le choix de certaines broches (par exemple la D9 pour le signal d'horloge de la carte à puce, les broches PWM pour les servos, les A4 et A5 pour le I2C, les A6 et A7 inutilisables en digital).

Modifier les branchements sur l'arduino c'est fastidieux et c'est prendre un risque de se tromper et de griller la carte.

Au début j'ai fait mes connexions comme je voulais car j'ai reçu le matériel et expérimenté au fur et à mesure et sur des arduinos différents sur plusieurs breadboard. Quand le temps est venu de mettre tout sur un seul arduino, le mieux a été d'utiliser EasyEDA pour faire le routing en prenant en compte toutes les contraintes. A un moment j'avais oublié les résistances de pull-up/pull-down et j'ai dû recommencé un bon morceau du circuit.

Le switch est sur la broche D13 mais il faut faire attention à ne pas activer le debug de SCLib car cette dernière s'en sert pour autre chose.

 - Penser à la taille des plaques de cuivres qu'on a, pour être sûr que ce qu'on fait à l'écran rentre bien ;
 - Utiliser des straps : placer des pads aux endroits où l'on veut strapper et passer sur le calque haut pour les relier (pas obligatoire mais cela permet de visualiser le trajet du strap).

### Gravure du PCB

1. Découpe du PCB : au cuter fort entailler la plaque des deux côté, la pincer entre deux plats et appuyer pour casser la plaque au niveau des coupes de cuter, un peu comme pour du verre. Puis poncer les bords ;

1. Imprimer le côté composant sur une feuille de papier glacé (la plus fine possible) du genre qu'on trouve dans certain magazine ou prospectus. La fixer sur une feuille d'imprimante avec du scotch bleu par exemple mais surtout pas avec du scotch plastique car il risque de fondre dans l'imprimante laser ;

1. Découper précisément au cuter sans toucher la surface imprimée avec ses gros doigts gras ;

1. Faire un test de positionnement sur le pcb ;

1. **A vérifier** Polir le côté cuivre très finement (au contraire de ce que l'on voit dans les tutos car lorsque j'ai fait l'impression du côté composant ça a bien mieux marché alors que la surface de l'époxy est très lisse).

1. Nettoyer la surface du cuivre avec de l'alcool isopropylique (ou ménager à défaut) jusqu'à ce que le chiffon reste propre. à partir de là ne plus toucher la surface du cuivre avec ses gros doigts gras ;

1. Verser du dissolvant Gemey Maybelline à la surface du cuivre en penchant légérement la plaque d'un côté puis de l'autre pour répartir le liquide à la surface. S'aider de son doigt PROPRE ou d'un ustensile propre pour s'aider ;

1. Positionner précisément le typon sans le faire gliser à la surface de la plaque ;

1. Tapoter légérement pour assurer le contact du typon partout. Il va foncer en s'imbibant. Si il reste des zones claire ajouter un peu de dissolvant mais cela ne devrait pas être nécessaire **(à vérifier)** ;

1. Poser un morceau de sopalin ou un mouchoir en papier, une plaque rigide et un poids par dessus. Maintenir une pression avec la main pendant 20s puis laisser reposer 10 min ;

1. Récupérer la plaque avec le typon qui est collé dessus, s'il est sec le laisser dans un bac d'eau pendant 10 min.

1. Peller le typon, il devrait s'enlever d'un seul tenant.

1. On peut nettoyer la surface légérement avec un peu d'alcool (surtout par d'acétone) sans appuyer ni incister pour avoir des pistes bien noires.

## Arduino
### La broche 13
La broche 13 est souvent reliée à une led soudée sur l'arduino. La LED est reliée à la masse et pour l'allumer il suffit de configurer la broche 13 en sortie et d'y envoyer un niveau HAUT.
Mais on peut se servir de cette broche pour autre chose, par exemple, pour y brancher un interrupteur. C'est ce que j'ai fait. J'ai configurer la broche en INPUT_PULLUP et je détecte les états HAUT et BAS de la broche en fonction de la position de l’interrupteur. Sauf que j'avais un niveau BAS quelque soit la position de l'interrupteur.

En fait, c'est à cause de la LED. La résistance qui y est associée est trop faible et relie la broche 13 en permanence à l'état BAS. Pour corriger cela, il faut ajouter une résistance de PULLUP externe d'au moins 1kOhms.

### Machine à état
J'ai commencé à coder de façon simple, assez linéaire. Mais assez rapidemment, je me suis retrouvé avec plein de booléens un peu partout pour contrôler le nombre de passages dans certains bouts de code et plus particulièrement pour savoir où j'en étais dans les étapes, dans quel état j'erre. 

Ce qui m'a conduit à coder mon programme grâce à une machine à état (simplifiée de chez simplifiée, un bon gros switch quoi). Pour une meilleur lisibilité, j'ai essayé autant que possible de faire les changements d'état dans le switch principal (parce que sinon c'est vite difficile de repérer le fil conducteur (cas nominal) du programme).

Cela m'a permis de résoudre des problèmes de répétitions non nécessaires d'exécution de code, comme par exemple afficher un message sur le LCD. Dans ce dernier cas, une seule exécution suffit à afficher et maintenir un texte, mais comme l'arduino passe dans sa boucle des millions de fois par seconde (ou pas loin), avec la machine à état j'ai un état qui affiche le message une fois et passe à un état suivant.

### Les pièces de monnaie pour tester
Ne les laissez pas trop près de l'arduino. Les pièces sont en métal, le métal est conducteur et les arduino n'aiment pas les courts-circuits.

# VSCode
## Configuration c++
Il a du mal à trouver les includes. Il faut les ajouter dans includePath et peut-être dans browse.path.
```
{
    "configurations": [
        {
            "name": "Win32",
            "includePath": [
                "C:\\Program Files (x86)\\Arduino\\tools\\**",
                "C:\\Program Files (x86)\\Arduino\\hardware\\arduino\\avr\\**",
                "C:\\Program Files (x86)\\Arduino\\libraries\\**",
                "C:\\Program Files (x86)\\Arduino\\hardware\\tools\\avr\\avr\\include\\**",
                "C:\\Program Files (x86)\\Arduino\\hardware\\tools\\**"

            ],
            "forcedInclude": [
                "C:\\Program Files (x86)\\Arduino\\hardware\\arduino\\avr\\cores\\arduino\\Arduino.h"
            ],
            "intelliSenseMode": "msvc-x64",
            "browse": {
                "path": [
                    "C:\\Users\\richa\\Documents\\Arduino\\libraries",
                    "C:\\Program Files\\arduino-1.8.9\\libraries",
                    "C:\\Program Files (x86)\\Arduino\\hardware\\tools"
                ]
            }
        }
    ],
    "version": 4
}
```

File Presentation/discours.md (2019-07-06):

# Distributeur Automatique d'Argent de Poche

<!-- Phrase d'introduction -->
## Phrase d'introduction

Il y a quelques mois, avec mon épouse, nous avons décidé de donner de l'argent de poche à nos enfants et, ce, malgré les terribles risques encourus...
 <!-- FIN -- Phrase d'introduction -->

<!-- Pause blagounette -->
# Pause blagounette


<!-- FIN -- Pause blagounette -->

<!-- Courte introduction à l'argent de poche et genèse du projet -->
## Courte introduction à l'argent de poche et genèse du projet

Nous avons fait comme beaucoup de parents pour qu'elles puissent commencer à apprendre à gérer leur argent, à en découvrir la valeur : qu'on peut l'économiser si on n'achète rien, que quand on en dépense on en a moins...

Néanmoins, même si c'est assez courant, j'ai quand même regardé dans la littérature ce qu'il s'en disait et j'ai découvert un certain concensus autour 5 "règles" :

1. La quantité est libre ;
2. 1 fois par semaine car une fois par mois c'est trop long pour eux, 1 fois par semaine est plus en accord avec leur échelle de temps et encore, au début elles oubliaient assez vite ;
3. On le donne tout le temps, même si elles ont fait un bêtise, une grosse bêtise voire même une trés trés grosse bêtise ;
4. Ce n'est pas une rémunération, en échange de tâches ménagères par exemple, elles touchent leur argent de poche de manière inconditionnelle (cela vient plus tard la notion de rémunération) ;
5. Elles dépensent leur argent comme elles l'entendent, exception faite de la drogue, des armes et autres produit récréatifs du même acabit. Personnellement, vu qu'elles ont des chambres déjà bien saturée, lorsqu'on fait un cide-grenier par exemple, je les invite à en faire le tour et à s'acheter 1 ou 2 objets maximum.

L'idée générale étant de pouvoir faire "comme les grands". Mais quitte à faire comme les grands, est-ce qu'on ne pourrait pas aller un peu plus loin avec un projet qui serait fun pour elles et fun pour leur papounet ?

C'est comme ça qu'est née l'idée d'un distributeur automatique d'argent de poche : fabriquer une machine dans laquelle elle inséreraient leur "carte bleue", saisiraient leur code secret en suivant les instructions à l'écran et regarderaient la machine se mettre en action pour distribuer les pièces une à une à l'aide d'un petit mécanisme...
<!-- FIN -- Courte introduction à l'argent de poche et genèse du projet -->

<!-- Le poussoir -->
## Le poussoir

### Version longue
...que je me suis empressé de concevoir.

C'est la première chose à laquelle je me suis intéressé parce que c'est la partie la plus concrète, on peut la voir, la toucher, la regarder bouger toute seule.

Au début, je m'étais inspiré d'une trieuse à pièce sur laquelle il y avait une sorte de corbeille remplie de pièces en vrac et une roue dans laquelle étaient aménagés des espaces pour accueillir une pièce à la fois. La roue, en tournant, capture une pièce et la dépose dans la trieuse. Je la voyait bien à l'horizontale sous une colonne de pièce. En tournant elle prendrait une pièce et la déposerait à l'endroit de la distribution. Mais ça manquait un peut de vie et la conception mécanique m'embêtait un peu : soit il fallait utiliser une vis sans fin avec une mauvaise maîtrise des mouvements à cause des jeux entre les différents éléments, ou alors en prise directe sur un moteur pas à pas mais je craignais de ne pas avoir suffisamment de puissance ou que cela consomme trop.

Et puis j'ai pensé au mouvement bielle-manivelle qu'on retrouve dans les moteurs à explosion et qui permet de transformer un mouvement de rotation en mouvement de translation (le piston dans le moteur). Le mouvement est sympas, presque hypnotique, les pièces sont faciles à concevoir et fabriquer et on peut connecter le tout à un servo moteur, de ceux qu'on utilise dans le modélisme, et qui sont commandables par un signal PWM facilement générale par l'*arduino*.

Mon premier essai a été de réaliser une impression en une seule "pièce" inspirée de ces impressions de dragons, serpents et autres robots articulés qu'on imprime en un seul bloc sans assemblage. Après quelques tâtonnements (et il y en a beaucoup en impression 3D, il ne faut pas hésiter à concevoir puis imprimer pour voir ce que cela donne) j'ai obtenu ce magnifique spécimen de bielle-manivelle en une seule impression.

Donc, j'ai réussi à imprimer le poussoir en une seule pièce et en plus, sans résistance au niveau des axes ce qui m'a permis de valider la puissance des servos de 9g et dun peu plus d'un kg de couple. J'ai assemblé un système rudimentaire et tenté de pousser une pièce de 2€ en bas d'une colonne de 25 pièces et ça a marché du premier coup.

J'ai un un système qui marche très bien, c'est cool mais ça manque de couleurs et mes filles sont très exigeantes en matière de couleurs flashy qui font saigner des yeux et en plus, une seule couleur ne permet pas de bien visualiser le mouvement des différentes pièces. Alors j'ai repris ma conception pour avoir des pièces indépendantes et pouvoir les imprimer chacune dans une couleur différente (je n'ai qu'une seule tête d'impression sur mon imprimante 3D). L'exercice est assez facile avec un outil comme fusion 360 mais la question la plus délicate était de savoir comment assembler ces éléments. 

La première idée est d'utiliser des écrous et des boulons pour maintenir les pièces entre elles et jouer le rôle des axes de rotations. Mais, d'abord, je trouve ça assez moche et je voulais au maximum utiliser du PLA en quantité la plus petite possible (le plastique c'est fantastique mais ça fait pas du bien à la planète bien que celui-ci soit biodégradable assez rapidement). Alors je me suis inspiré des légos techniques : ils des petites pièces qui permettent d'assembles les élements entre eux et même servir d'axe de rotation. Elles ont la particularité d'être fendues sur un diamètre ce qui leur donne de la flexibilité pour les enfoncer dans les trous et à leur extrémité un bourelet permer de s'accrocher à la pièce lorsque cette attache se détend en sortant du trou.

**Et ça donne ça (image du poussoir en éclaté)**

Là aussi on travaille par tatonnement. Par exemple, sur cet ensemble le mouvement est dur. D'une par parce que la pièce est voilée : il faut attendre que la température du plateau soit redescendu sinon, la pièce encore chaude de déforme et garde le pli. D'autre part parce que les jeux que j'avais mis étaient trop serrés.

À l'impression on prend garde à imprimer la pièce de telle sorte que les efforts de flexion soient perpendiculaire aux couches d'impression pour plus de solidité.

C'est important de garder à l'esprit la méthode que l'on va employer pour imprimer en 3D au moment où on fait la conception dans le logiciel 3D ET au moment du slicing. Par exemple, si on observe le premier poussoir en une seule fois on remarquera que l'extrémité inférieur du poussoir arrive au ras du disque de maintient, qui est lui-même d'un diamètre égal à la largeur de la bielle : parce qu'en fait, **cette pièce s'imprime comme ça**.

**Montrer la pièce physique, en l'assemblant devant l'assistance**

### Version courte
...que je me suis empressé de concevoir.

C'est un mécanisme bielle-manivelle qui transforme un mouvement de rotation en mouvement de translation (ou rotation) alternatif, le même qu'on retrouve dans nos moteus à explosison pour activer le piston. 

==> Slide du mouvement (passer rapidement)

J'ai choisi ce mécanisme parce que j'aime bien le mouvement, je le trouve assez hyptnotique et il est facile à concevoir.

==> Slide du mécanisme fixe

Le mécanisme est constitué de plusieurs éléments : on retrouve la manivelle qui transmet le mouvement et qui est reliée à un servo-moteur (un servo-moteur c'est un moteur qui est asservi, en position ici), la bielle qui permet de transformer le mouvement et le poussoir qui va effectuer le mouvement (éjecter les pièces).
Je pourrais voue parler de ce mécanisme pendant une heure tellement il y a de chose à en dire mais je vais passer rapidement sur les éléments essentiels.

Par exemple, ici c'est l'emplacement de la vis qui permet de relier la manivelle au servo moteur, pour que la tête de vis ne gêne pas le mouvement j'ai fait un petit alésage. Là, c'est pour accèder à cette vis quand on pose ou dépose le mécanisme. Au début, je ne l'avais pas fait et j'installais les pièce en "forçant". Et enfin, il y a les axes qui jouent à la fois le rôle d'axe de rotation mais également de maintient des pièces entre elles.

Pour les réaliser, je me suis inspiré des lego techniques. Une brique ressemble à ça, elle est percée de trous, dans lesquels vient s'insérer ce genre d'axe, fendu en son milieu pour lui donner plus de flexibilité et flanqué d'un petit bourelet pour qu'il reste bien en place.

Après quelques essais pour trouver les bons paramètres pour avoir assez de jeu mais pas trop, assez de flexibilité etc. Je suis arrivé à cette pièce là.
<!-- FIN -- Le poussoir -->

<!-- Clip -->
## Clip
==> Slide poussoir éclaté

On retrouve un plateau supérieur ainsi qu'un petit bourelet inférieur pour maintenir les pièces ensemble et la fente pour avoir suffisamment de flexibilité.

Quand on fait un design 3D en vu d'une impression en 3D il faut toujours garder à l'esprit comment on va imprimer la pièce.

*Détacher le poussoir et monter les différentes façon d'imprimer et les conséquences.* 

==> Slide impression clip
*Expliquer pour l'axe.*

Une fois imprimé comme ça on retire les supports, il peu y avoir un peu de travail à faire au niveau des pates d'éléphants et ça s'insère très bien dans les différentes pièces bielle/manivelle et manivelle/poussoir.

Pour que le poussoir ait un mouvement rectiligne il faut le contraindre dans cette direction. Et puis, il faut aussi lui ajouter le servo qui va engager le mouvement de rotation de la manivelle et puisqu'on y est, il faut aussi ajouter la réserve de pièces à distribuer grâce au poussoir. 
<!-- FIN -- Clip -->

<!-- Le support -->
## Le support
==> Slide support

Alors je vous présente le support sur lequel le servo vient se fixer, qui présente un guide rectiligne pour le poussoir au bout duquel on retrouve le réservoir à pièces.

Ici on retrouve l'espace dans lequel va se placer le servo-moteur avec les trous des vis de fixation qui vont bien. Pour avoir les bonnes mesure je me suis servi de la datasheet du servo et d'un pied à coulisse. Ça a marché du premier coup sauf sur le diamètre des trous qui était trop petit.

Là le rail pour guider le mouvement du poussoir et enfin le réservoir à pièces. Même cette partie n'est pas si triviale que ça.

D'abord, je voulais que le chargement des pièces se fasse bien, que les pièces ne restent pas coincées. Pour cela, il faut prendre non pas le diamètre de la pièce mais la diagonale entre ses deux faces plus une petite marge. Bon, en fait la hauteur de la pièce est tellement petite devant son diamètre que c'est un peut *kifkif bourrico* et au final, pour une pièce qui fait 25.75, on compte 26mm et on rajoute 0.5 de chaque côté.

Ce 0.5 mm de marge c'est ce qu'on recommande de prendre comme jeu pour les différents types d'assemblage. Mais il faut tester.

L'ouverture pratiquée à la sortie fait 3 mm, la hauteur d'une pièce de 2€ fait 2.2mm, à caus des imprecisions d'impression que la pièce va pouvoir sortir sans contrainte tout en assurant que la pièce du dessus ne soit pas emportée à cause des frottement ni au moment de l'extraction de la pièce inférieur ni au moment du retour du poussoir à sa position initiale.

ça c'est pour des pièces de 2€ et ça fonctionne bien jusqu'au pièces de 10 centimes. Mais la colonne de pièce est un peu en vrac, c'est trop large. Du coup je ferais une conception paramétrique pour généré un support sur-mesure.

Dans cette colonne j'ai pratiqué une rainure pour pouvoir récupérer facilement les pièces (notamment quand on par en vacance, quand le distributeur est plein il y a plus de **75€**, en plus de pouvoir visualiser la quantité de pièces restantes). 

**Montrer le mécanisme complet**
On a donc un mécanisme complet qui permet de distribuer des pièces de monnaies : un distributeur par valeur faciale.

Il ne reste plus qu'à le commander.

Et on va faire ça grâce à un arduino.
<!-- FIN -- Le support -->

<!-- Arduino -->
## Arduino 
J'ai choisi d'utiliser un arduino nano d'une part parce que c'est très facile à programmer, il y a une grosse communauté derrière, il est vraiment compact, ce qui permet de l'intégrer facilement sur un PCB soit en le soudant directement (mais je ne le recommande pas) soit en utilisant des connecteurs HE14 à un rang qui permettent de récupérer l'arduino pour le mettre à jour ou s'en servir sur un autre projet. 

Et, d'autre part, parce que par un coup de bol incroyable, il contient tout juste suffisament d'entrées/sorties pour le projet dans son ensemble.

Un arduino c'est basé sur un microcontrolleur. 

Un microcontrolleur, en gros c'est un petit processeur comme celui qu'on a dans nos machines, avec de la RAM, de la ROM, des controlleurs en tout genre et tout ça sur une seule puce. Il y en a de plusieurs types, les plus connus sont les PIC et les AVR.

Avant, c'était assez compliqué et chez de programmer un microcontrolleur parce que si le composant en lui-même est trés bon marché, le programmateur, lui était plustôt assez cher et en plus pas compatible avec tous les modèles. Le programme lui devait être écrit en C bas niveau ou en ASM au pire.

Avec les arduino, plus besoin de programmateur, on branche l'arduino sur un port usb, on code en C++ avec des librairies de haut niveau et en cliquant sur un bouton le programme se téléverse dans l'AVR (oui parce que sur les arduino ce sont des µC de type AVR).

Avec ces librairies on peut par exemple commander un servo. Et c'est simple si on a un servomoteur qui se contrôle avec une commande PWM. Ici c'est le cas.
<!-- FIN -- Arduino -->

<!-- PWM -->
## PWM
Le PWM sert à générer une tension continue à partir d'un signal carré. La valeur de la tension varie en fonction du rapport entre la durée d'une impulsion et la période du signal.
<!-- FIN -- PWM -->

Pour un servo commandable en PWM, un niveau de signal correspond à une position angulaire. 

Si on lui envoi 0 il va à la position 0 et essai d'y rester (ce sont des servos de modélisme qui sont asservi en position). Si on lui envoi du 180 il fait une demi-rotation et cherche à y rester (attention, j'ai des servo qui ont une amplitude de 180°, d'autres sont plus large et d'autre plus ressérés. Dans ce cas, il faut bien connaître les propriétés de son servo car si on lui envoi une commande qui va au-delà de ses capacités il risque de forcer, le courant va augmenter fortement et l'arduino et le servo risquent de griller).

**présentation du code**

__**description code broche pwm**__

Au départ, j'ai utilisé ce code comme ça. Mais j'ai eu un problème d'ordre sonnore : tant qu'on écrit un signal sur le servo, lui, il essai de maintenir sa position. Et comme ce sont des servo à pas cher ils ont tendance à osciller autour de leur position de référence et ça fait du bruit. Vu que le DAAP va se trouver dans le salon, c'est pas top. Au début je me suis dit que j'allais commander l'alimentation des servos via l'arduino mais dans mon cas ça fait prendre 3 pattes supplémentaires et trois transistors supplémentaires. Et puis j'ai fait un truc incroyable : j'ai lu la doc !

Et on découvre qu'il y a une méthode qui s'appelle `Servo::detach()` et qui permet de "déconnecter" le servo de la patte à laquelle il est attaché. Et c'est magique, plus de bruit.

==> Slide blanc

On a donc trois petits distributeurs qui attendent qu'on leur disent combien de pièces chacun doit distribuer.  La somme d'argent est libre du moment que c'est une combinaison des pièces disponibles. Mais on ne va pas stocker la combinaison des pièces mais la somme d'argent à distribuer. C'est à partir de ce nombre qu'il faut reconstituer la séquence de distribution.

Dans mon code, j'ai une liste de pousseurs de monnaie, chacun associé à une valeur faciale. Pour reconstituer la séquence de distribution je compte combien de fois on peut trouver la valeur faciale du distributeur courant dans le montant qu'il reste à distribuer et je place dans la séquence ce pousseur autant de fois. Ensuite je le montant restant et je recommence avec la valeur faciale du pousseur suivant jusqu'à ce que je ne puisse plus.

La distribution consiste à parcourir la liste sequence en appelant à chaque fois la méthode `CoinPusher::pushCoin()`. Ça permet de reconstituer le montant à distribuer.

Ce montant doit être stocké quelque part soit dans le code soit dans une mémoire extérieure.
Le problème qu'on rencontre en stockant ce montant dans le code c'est de réussir à retrouver à quel enfant il appartient. On peut se dire que le code secret est en fait l'identifiant unique de l'enfant mais c'est moche et ce n'est pas hyper fun. L'autre solution c'est de le stocker dans une mémoire extérieure que l'enfant pourrait conserver avec lui et  qui pourrait contenir toutes les informations liées à la distribution : le nom de l'enfant, le montant de l'argent de poche pour cet enfant et le code secret de l'enfant. Ça évite de devoir flasher l'arduino chaque fois que l'argent de poche change ou que l'enfant à oublié son code ou que le petit dernier a enfin le droit, lui aussi, de pouvoir acheter ses amis. 

Et pour ça il y a une super mémoire : la carte à puce.

<!-- SLE 4442 -->
Ce modèle est une SLE4442, une carte à puce sécurisée, c'est-à-dire que pour pouvoir écrire dedans où accéder à certaines zones mémoire il faut disposer du bon code pin, qui par défaut est FFFF, c'est pratique de le savoir quand on commence à expérimenter avec ce type de carte, surtout quand on sait qu'après trois mauvaises saisies la carte devient inutilisable. Pour la relier à l'arduino on utilise un connecteur de ce type qui est un simple boitier avec des broches souples qui viennent en contact des contacts dorés de la carte à puce. On y trouve également un petit intérupteur qui permet de détecter la présence de la carte.
<!-- ---FIN--- SLE 4442 -->

<!-- Structure carte -->
Ce code pin n'est pas le code de l'enfant, il pourrait, mais j'ai choisit de ne pas le faire par soucis de simplicité. Pour écrire les infos à l'intérieur de la carte j'ai créé un petit programme indépendant du projet, avec une petite interface avec le Serial de l'arduino qui permet de consulter le contenu de la carte et aussi d'y inscrire les données qu'on a besoin : le code secret, le montant de l'argent de poche, le nom de l'enfant mais aussi le nombre de caractères du prénom de l'enfant.

Même si en C/C++ il existe des méthodes de manipulation de chaines de caractères, ici je ne peux pas les utilser car c'est moi qui doit écrire dans la carte octet par octet et, pour une raison que j'ignore encore, j'ai eu un soucis en tentant d'écrire la valeur 0 dans la carte. Je pense que c'est un fausse manip mais pour avancer j'ai retenu cette solution-là.
<!-- ---FIN--- Structure carte -->

<!-- Discours trouver la librairie SClib-->
Ça peut paraître facile comme ça, et ça l'est dès qu'on a trouvé la bonne librairie. Et ça a été compliqué de trouver la bonne librairie. J'ai même faillit abandonné alors que je n'en trouvais pas et que l'implémentation du protocole dans un librairie maison constitue un projet en soi. Il faut manipuler des timers, il faut manipuler l'AVR en programmation bas niveau, c'est une tâche assez complexe. Mais à force de persévérence, je suis tombé sur une librairie, **sclib** qui n'a plus été touchée depuis 2015 mais ce n'est pas grave elle marche du feu de dieu. Elle permet normalement de travailler avec toutes les cartes de type SLE44X2 (carte sécurisé, synchrone ou pas). Elle est plutôt bien fichu, notamment parce qu'on peut, à l'aide d'un `#define` supprimer du code généré toute la partie concernant les cartes asynchrone ce qui allège fortement la taille du programme à téléverser dans l'arduino. Cette librairie implémente le protocole pour la SLE 4442 et...
<!-- FIN -- Discours trouver la librairie SClib-->

<!-- Protocole SLE4442 -->
... pour illustrer rapidement comment ça marche voici ce qu'il se passe lorsqu'on insère la carte dans le connecteur de carte à puce.

Donc ça c'est une partie de ce qu'il se passe lorsque l'enfant insère la carte dans l'appareil qui, par ailleur,  l'y invitait poliment par l'intermédiaire de l'écran LCD.
<!-- FIN -- Protocole SLE4442 -->

<!-- Présentation de L'écran LCD -->
C'est un écran à fond bleu conçu pour bousiller la rétine des enfants, il faut les habituer tôt. Mais surtout il permet d'afficher 4 lignes de 20 caractères (les fameux 20 caractères max du prénom que l'on stocke dans la carte à puce, si vous vous souvenez bien), je voulais un gros écran parce qu'en général les écrans LCD sont assez petits surtout si on se laisse tenter par les magniques écrans OLED polychromes, qui eux, sont franchement rikikis.

À la base, pour commander cet écran, il faut prévoir 6 broches sur l'arduino avec les librairies à disposition. Ça fait beaucoup, chaque broche de l'arduino est précieuse et donc il faut toujours passer un peu de temps à chercher si il y a un moyen de diminuer ce nombre de broches. Il se trouve que pour ce type d'écran il existe un petit modeil qui permet de communiquer avec lui en utilisant le protocole I2C qui, lui, n'utilise que deuxx broches de l'arduino. Et non seulement, l'implémentation de ce protocole est fournie par défaut avec l'arduino (c'est la librairie Wire) mais en plus, l'arduino possède (pour le nano) deux broches dédiées à cette fonction. Ce sont les broches SDA et SCL qu'on retrouve sur les diagrammes de *pinout*.
<!-- FIN -- Présentation de L'écran LCD -->

<!-- Introduction au protocole I2C -->
La norme I2C c'est un protocole de communication série, un peu comme l'USB. C'est un gros gros gros standard industriel implémenté par une grosse grosse grosse quantité d'équipements. On le retrouve partout. C'est basé sur une communication maître-esclave exclusive. Le ou les maîtres sont connectés via les ligne SCL/SDA aux différents esclaves. Le principe consiste à ce qu'un maître emette une condition START, tous les esclaves écoutent, le maître transmet alors l'adresse de l'esclave auquel il souhaite s'adresser (chaque composant dispose de sa propre adresse codée sur 7 bit) le 8ème bit permet de préciser s'il veut envoyer des données ou en recevoir. 

Autant dire que je suis bien content de ne pas avoir à l'implémenter. Maiiiiis ce serait intéressant !
<!-- FIN -- Introduction au protocole I2C -->

<!-- Librairie LCD -->
On a trouvé un composant qui réduit le nombre de broches, mais ça ne ne signifie pas pour autant qu'il existe une librairie qui va bien. On a de la chance, la communauté arduino est plutôt riche, et il se trouve qu'il en existe plusieurs. Par contre, il faut tester parce que toutes ne se valent pas. J'ai dû en essayer plusieurs, entre celles qui vendent du rêve, celles qui sont obsolettes et celles qui ne remplissent pas toutes les fonctions j'ai quand même fini par trouver la perle rare faite par un certain **Mathias Hertel**. 

Elle marche et en plus elle est simple d'utilisation : après avoir déclarer l'include qui va bien (pensez à donner des indices sur comment retrouver la livrairies, l'auteur, le nom dans la bibliothèque ou encore la version) il suffit de créer une instance de l'écran en précisant l'adresse I2C où le trouver puis d'écrire le texte qu'on veut là où on lui indique. Il y a également des fonctions utilisaires pour effacer l'écran par exemple. 
C'est le genre de fonction qu'on va utiliser pour changer le message à l'écran, pour, par exemple, inviter l'enfant à saisir son code une fois qu'il a inséré sa carte...
<!-- FIN -- Librairie LCD -->

<!-- Clavier matriciel -->
...La saisie du code se fait grace à un petit clavier matriciel de ce type, à 16 touche, 4x4. Là, niveau broche c'est du lourd parce qu'il en faut 8 : 1 pour chacune des 4 lignes et 1 pour chacune des 4 colonnes.
Ce genre de clavier fonctionne ainsi :

C'est un ensemble d'interrupteurs. L'arduino va allumer tour à tour chaque colonne par exemple. Et dans le même il va scanner chaque ligne. Lorsqu'il allume la colonne 2 et que il détecte un signal sur la ligne 3 c'est que la touche 8 a été préssée. Il peut même détecter plusieurs touche en même temps.
Et il répète cette opération trés rapidement <!--tout en prenant en compte le rebond des touches. -->

On commence à avoir un système plutôt complet : un distributeur, une IHM, une carte avec toutes les infos pour la distribution et un arduino pour contrôler tout ça.

Mais, si vous vous souvenez, il y a une règle qui dit qu'on doit distribuer l'argent de poche qu'une seule fois par semaine. Alors il faut pouvoir connaître la date et pour ça il y a l'horloge temps réél.
<!-- FIN -- Clavier matriciel -->

<!-- Le rebond 
Le rebond, c'est un phénomène qui se produit sur les composants mécaniques généralement, et souvant sur les interupteurs/bouton poussoir. Le contact n'est jamais franc, les pièces ont tendances à rebondir les unes sur les autres provoquant une signal aléatoir interprété comme une série de 0 et de 1 consécutifs (dont d'appui et de relachement du bouton) pendant un temps très court. Mais à 16 MHz, ce qui est court pour un humain est long pour un arduino qui les détecte tous. On peut implémenter un antirebond de manière électronique en insérant des filtres de type RC ou en l'implémentant de manière logicielle comme dans la librairie keypad.
<!-- FIN - Le rebond -->

<!-- RTC -->
## RTC
C'est un DS3231 embarqué sur un petit module qui permet de le relier à l'arduino en I2C, pour une fois on a du bol.

On pourrait se demander si il n'y a pas déjà une fonction qui permet d'obtenir un timestamp sur arduino. En fait même sur les PCs c'est un composant à part. Il y a bien une fonction getMillis() qui compte le temps qui s'est écoulé depuis le démarrage de l'arduino et on pourrait imaginer fournir un timestamp à l'arduino via le clavier mais ce n'est pas très joli et en plus ce temps est stocké dans un registre de 32 bits et tous les 50J environs il y a un overflow et le compteur revient à zéro.

Donc on utilise une horloge temps réélle. Sur ce modèle il y a une pile et aussi une fonction de recharge, c'est une pile bouton rechargeable (LIR2032), je ne savais même pas que ça existait.

On aurait pu utiliser un RTC un peut moins cher, le DS1307 mais il est moins précis, il perd plus d'une seconde par jour.

Alors que le DS3231 ne perd pour ainsi dire rien car il est accompagné d'un capteur de température qui corrige la dérive due aux changements de température. Ce capteur est même intérrogeable et il y a également une petite EEPROM. Tous ces composants sont visible quand on utilise le I2C scanner dans les programmes d'exemples.

Que ce soit le DS1307 ou le DS3231 il existe des librairies pour communiquer avec. Et, on a l'habitude maintenant, c'est très facile à utiliser. 

==> Slide du code

On notera qu'ici, point d'orienté objet, c'est une bon vieux `struct`.

On a maintenant un système complet. Mais, il ne faut pas oublier qu'on va mettre ça entre les mains de petits hackers en herbe et que ces brigands vont probablement prendre un malin plaisir à tenter de contourner le système.

En vrai, j'ai plutôt confiance mais c'était une occasion en or de pouvoir utiliser l'EEPROM.
<!-- FIN -- RTC -->

<!-- EEPROM -->
## EEPROM
Pour le coup, si l'api est simple d'utilisation il faut gérer soit même la mémoire.
<!-- FIN -- EEPROM -->

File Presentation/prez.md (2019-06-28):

---
pagetitle: DAAP
lang: fr-FR
---

# Distributeur Automatique d'Argent de Poche

Richard Fagot

:::notes
1. Tiens-toi bien ;
1. Pense à ta première phrase ;
1. Prend une inspiration ;
1. Embrasse la salle d'un regard et lance-toi.
:::

# 


::: notes
Passer rapidement.
:::

#
::: notes
Histoire du projet

- Décision de donner des sous aux enfants ;
- Règles de l'argent de poche ;
- Quitte à faire comme les grands autant aller jusqu'au bout ;
- Projet fun pour les enfants ;
- (et fun pour le papa).
- Présenter le workflow.
    
:::

# Roue trieuse
::: notes
- Roue trieuse ;
- ==> pas assez sexy.
:::

# 


::: notes
**Le poussoir **

- http://subaru.univ-lemans.fr/AccesLibre/UM/Pedago/physique/02/meca/bielle.html
- conception 3D fusion 360 ;
- Impression en une fois ;
- Puis en plusieurs pièces pour pouvoir avoir plusieurs couleurs ;
- Raffinement à cause de la nouvelle visserie des servos
- Clipper les pièces ensembles ;
- ==> mécanisme retenu.
:::

#


::: notes
**Assemblage des axes**

- Sens d'impression ;
- ==> Liaison ???
:::

#


::: notes
- colonne de pièces ;
- guidage du poussoir ;
- ==> Support du servo
:::

#

::: notes
**Servomoteur**

- force ;
- bruit du maintient en position.
:::

#


::: notes

:::

# 


::: notes

:::

# Fusion 360
Demo !

::: note
- Extrusion et opérations booléénes
- liaisons
- les contraintes de l'impression 3D (porte à faux, résistance)
:::

# Slicing
Demo !

# Le système de saisie
- écran / clavier

# Gestion de l'heure
-RTC

# L'impression 3D

# L'Arduino
Le C++ c'est l'enfer : déclaration d'un int et d'un char [20] mais lecture de 21 caractère écrase une partie du int.
```cpp
void setup() {

}

void loop() {

}

```

# My Little Hackers
Empêcher les enfants de hacker le système

# Évolution

- Transformer les distributeurs en petits robots autonomes.
- DAAP Reloaded : Coder en arduino avec **Rust**
- Ajouter un configurateur (nombre de distributeurs, valeur faciale, actualiser l'heure **/!\ à la qté de String**)
- Editer une carte à puce directement via le DAAP.

::: notes

Transformer les distributeurs en petits robots automnomes (par exemple avec une tête de chat) placés dans une petite niche.
Quand l'enfant insère sa carte ils se mettent à trépigner d'impatience.
Une fois la carte retirée ils foncent vers un bol pour cracher par leur petite bouche les pièces qu'il faut.

:::

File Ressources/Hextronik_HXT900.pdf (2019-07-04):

# Hextronik HXT900 - 9g Micro Servo


Basic Information

Modulation: | Analog
Torque: | 4.8V: 22.2 oz-in (1.60 kg-cm)
Speed: | 4.8V: 0.12 sec/60°
Weight: | 0.32 oz (9.1 g)

Dimensions:

Length:

### 0.83 in (21.0 mm)

Width:

### 0.47 in (12.0 mm)

Height:

### 0.87 in (22.0 mm)

Motor Type: | Coreless
Gear Type: | Plastic
Rotation/Support: | Bushing

Additional Specifications

Rotational Range: | 90°
Pulse Cycle: | 20 ms
Pulse Width: | 450-2450 µs
Connector Type: | JR

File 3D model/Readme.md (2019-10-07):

Export des modèles 3D pour *Fusion 360*.

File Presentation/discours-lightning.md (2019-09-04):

J'espère que vous êtes bien installé. On m'a dit que j'avais deux heures, mais je dépasserai un petit peu.

Il y a quelques mois de cela, nous avons décidé avec mon épouse de donner de l'argent de poche à nos enfants malgré les terribles risques encourus.

<!-- Extrait BD de Calvin & Hobbs-->

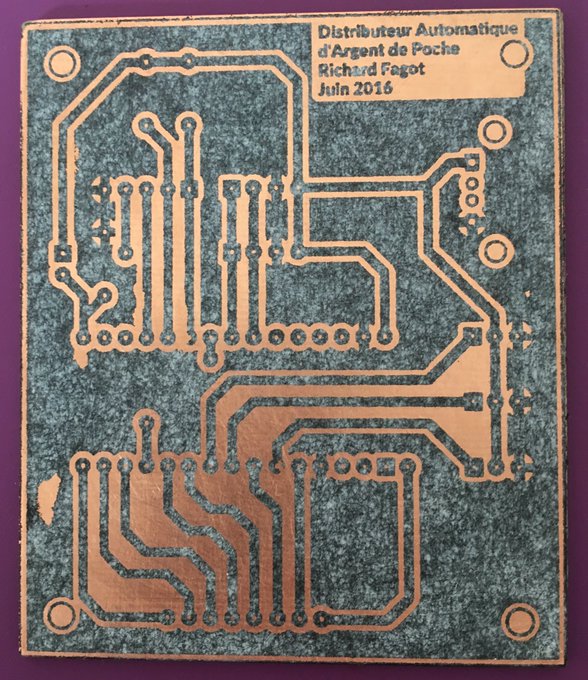
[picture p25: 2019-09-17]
Presentation/assets/img/PCB après transfert.jpg

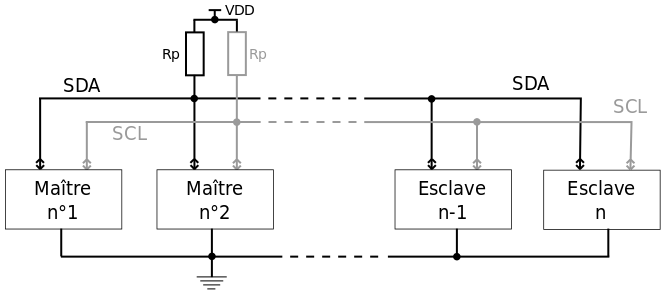
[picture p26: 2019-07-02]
Presentation/assets/img/I2C - M-E.png

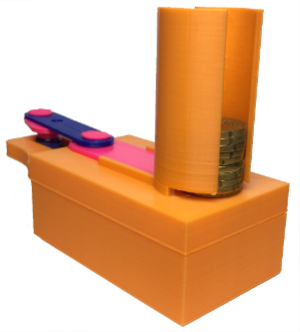
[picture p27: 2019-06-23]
Presentation/assets/img/distrib.png

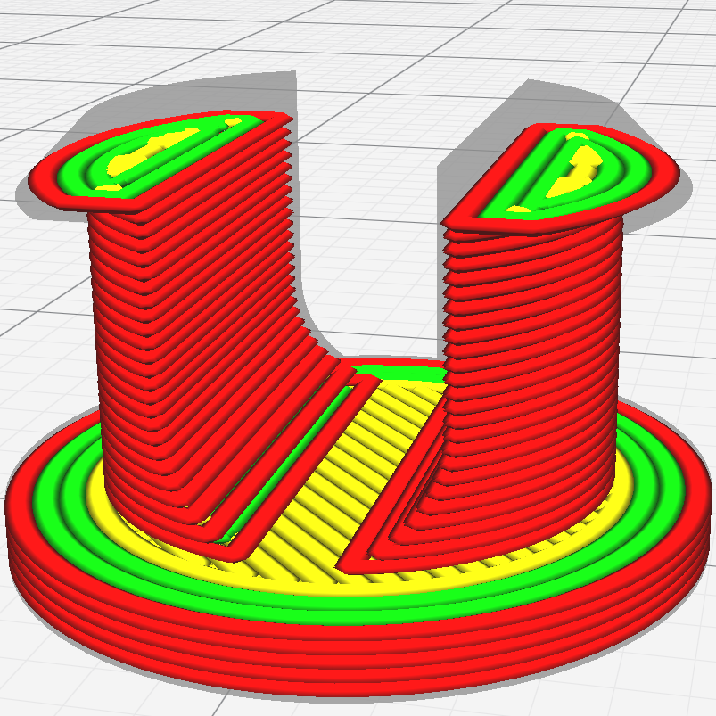
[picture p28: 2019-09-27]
Presentation/assets/img/clip-naturel-porteàfaux.png

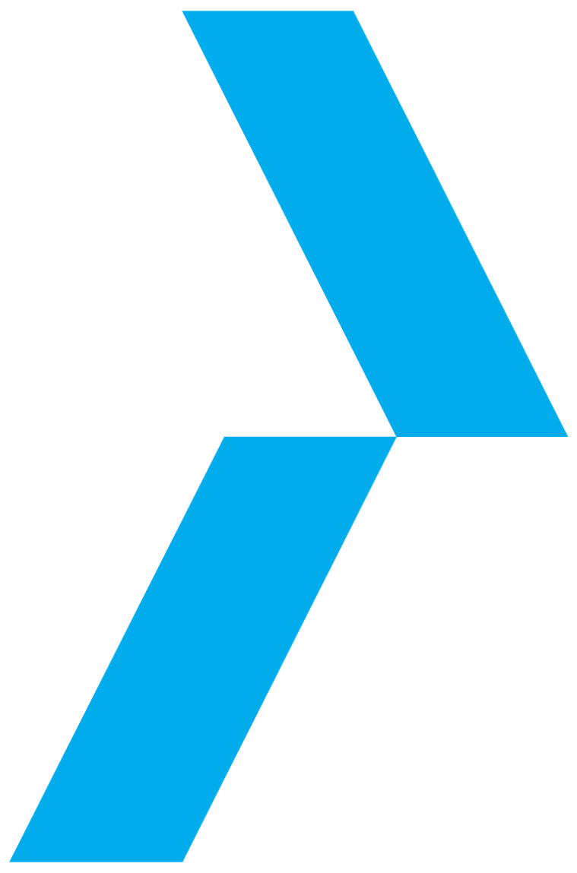
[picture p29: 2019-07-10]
Presentation/assets/img/viseo.png

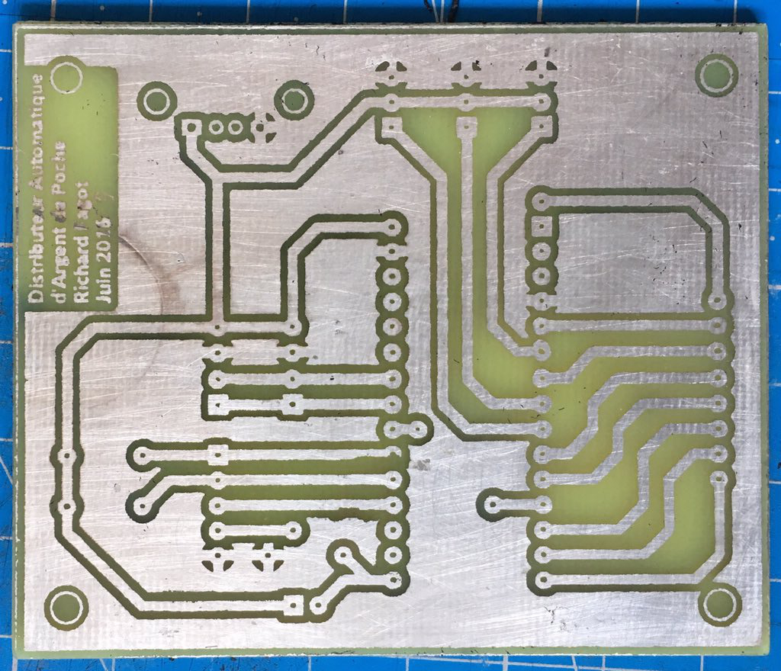
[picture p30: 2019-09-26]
Presentation/devfest-2019/assets/img/PCB étamé.jpg

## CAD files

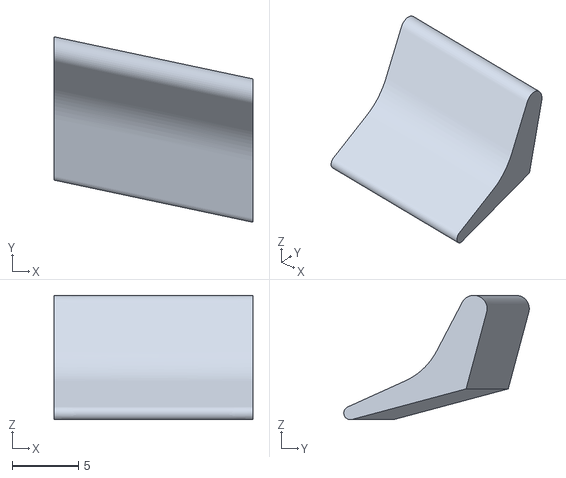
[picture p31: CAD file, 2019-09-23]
Fichiers STL/Antichutte.stl
15.0 x 14.0 x 9.37

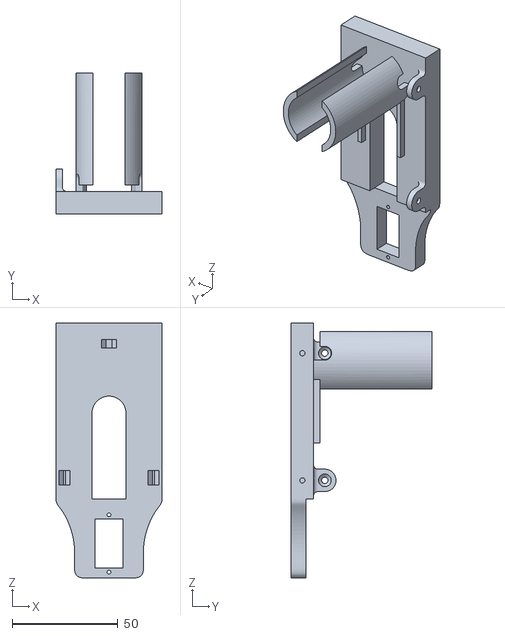
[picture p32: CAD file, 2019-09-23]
Fichiers STL/réservoir 1 euro.stl
50.0 x 66.4 x 120.3

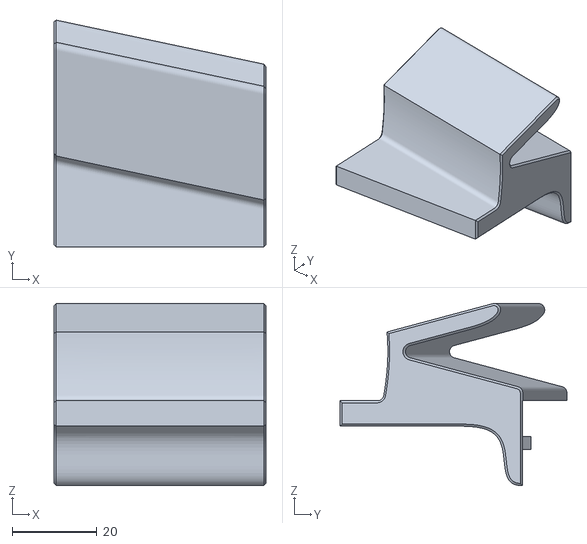
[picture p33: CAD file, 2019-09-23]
Fichiers STL/Rail petit.stl
50.0 x 53.5 x 42.9

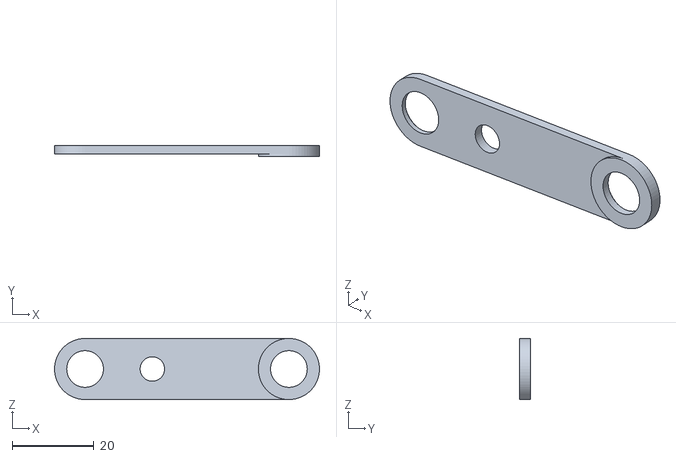
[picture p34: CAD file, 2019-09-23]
Fichiers STL/Bielle v2.stl
65.0 x 2.60 x 15.0

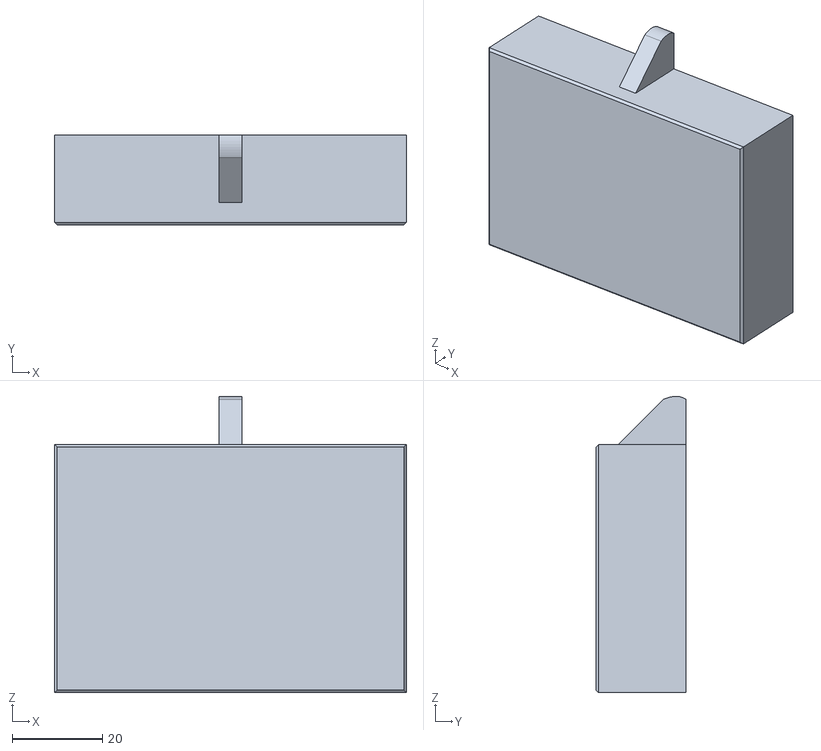
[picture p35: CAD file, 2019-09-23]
Fichiers STL/Tiroir.stl
78.0 x 20.0 x 65.7

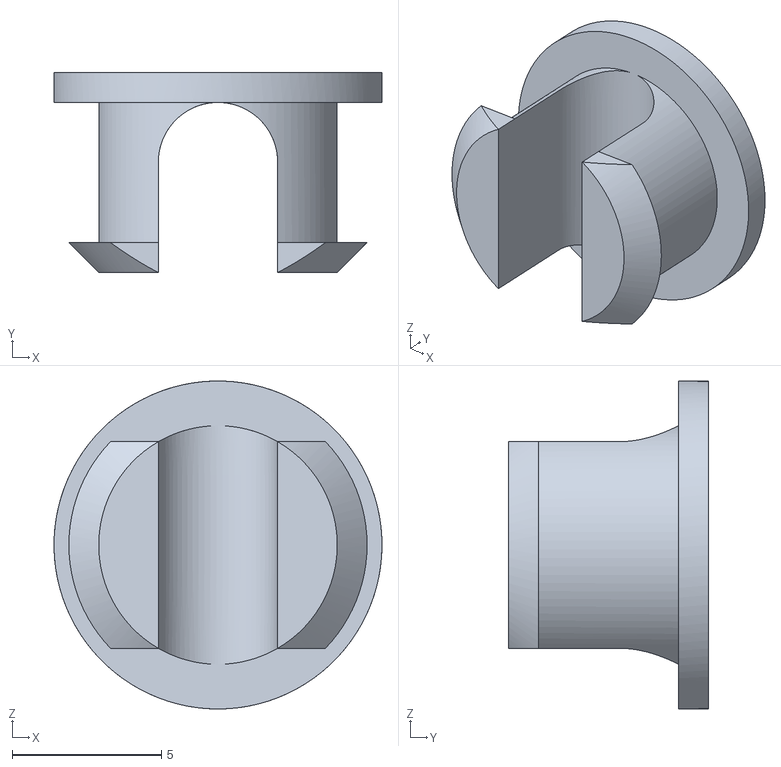
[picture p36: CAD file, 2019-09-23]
Fichiers STL/Clips v2.stl
11.0 x 6.70 x 11.0

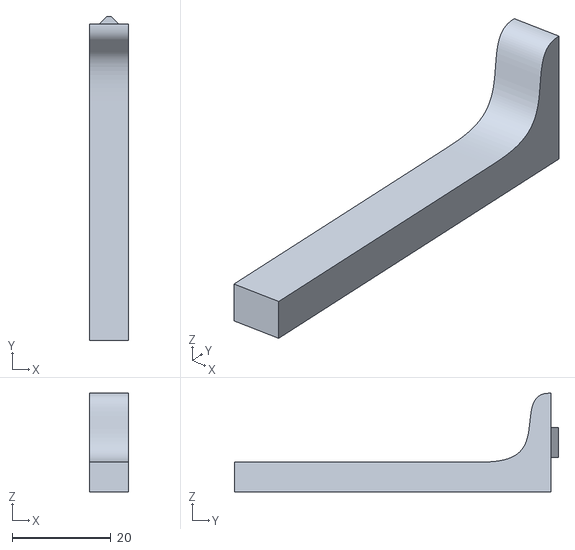
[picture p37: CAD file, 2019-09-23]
Fichiers STL/Patte arrière grande.stl
8.00 x 65.7 x 20.0

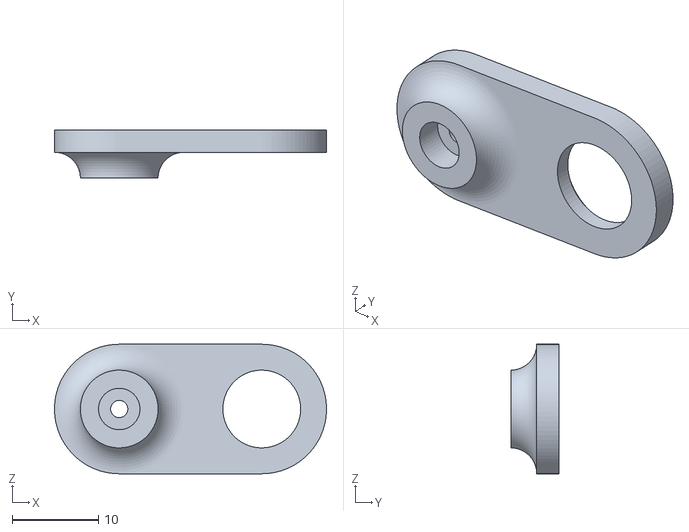
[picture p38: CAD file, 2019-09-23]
Fichiers STL/manivelle v2.stl
31.5 x 5.60 x 15.0

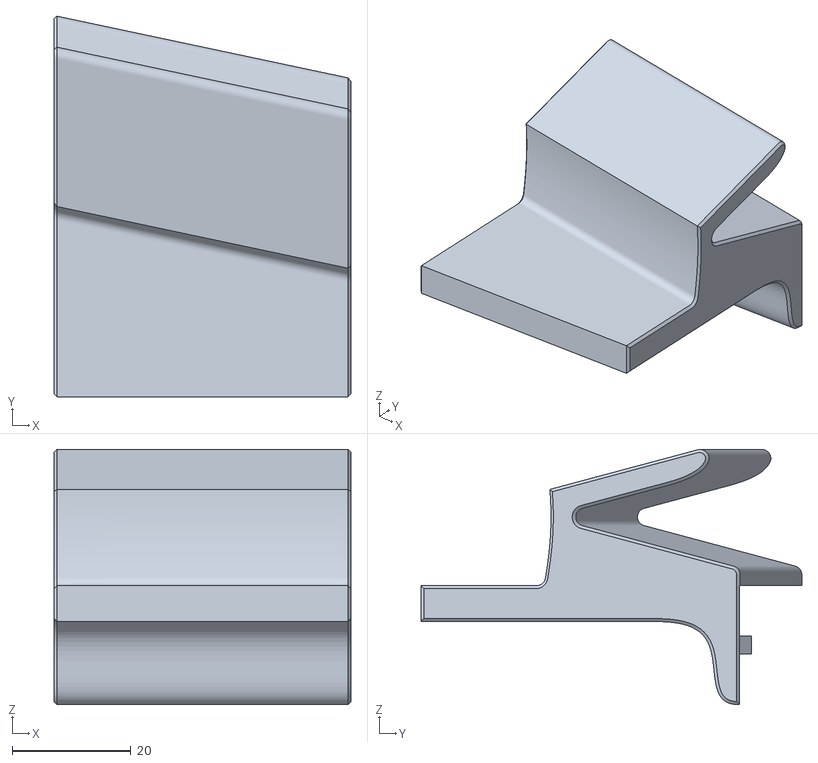
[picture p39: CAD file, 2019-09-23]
Fichiers STL/Rail moyen.stl
50.0 x 64.1 x 42.9

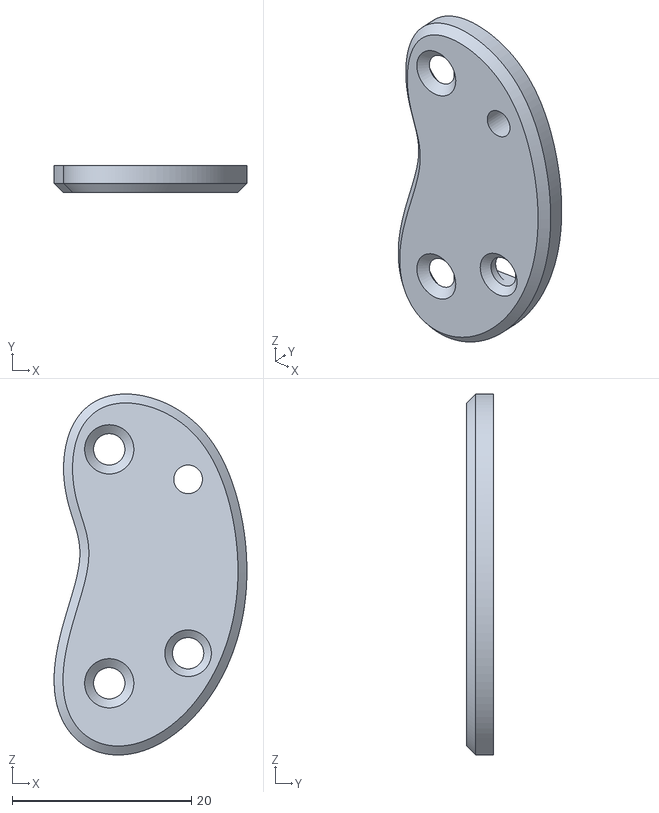
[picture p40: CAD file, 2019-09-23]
Fichiers STL/Platine Gauche.stl
21.5 x 3.00 x 40.3

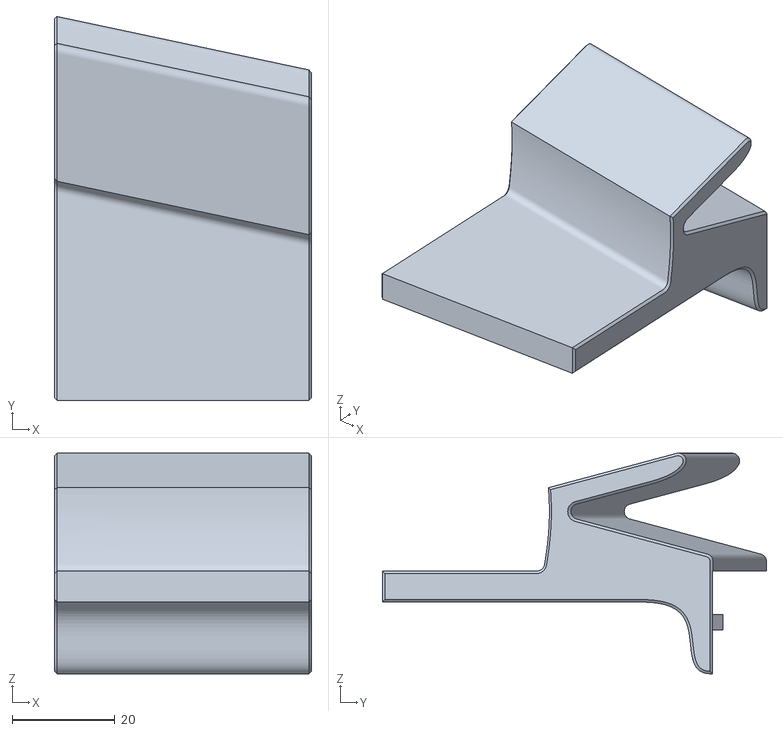
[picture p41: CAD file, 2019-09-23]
Fichiers STL/Rail haut.stl
50.0 x 74.7 x 42.9

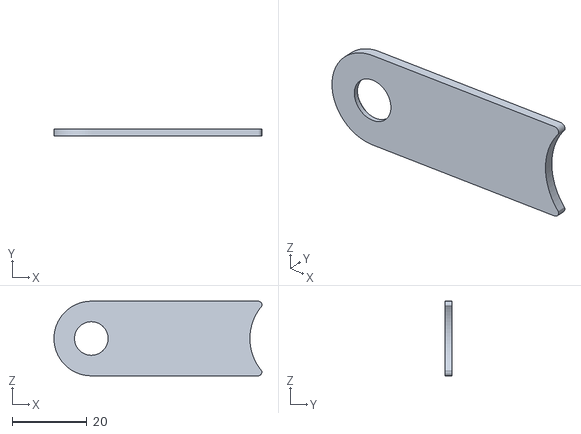
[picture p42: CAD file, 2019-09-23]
Fichiers STL/Poussoir.stl
55.7 x 2.00 x 20.0

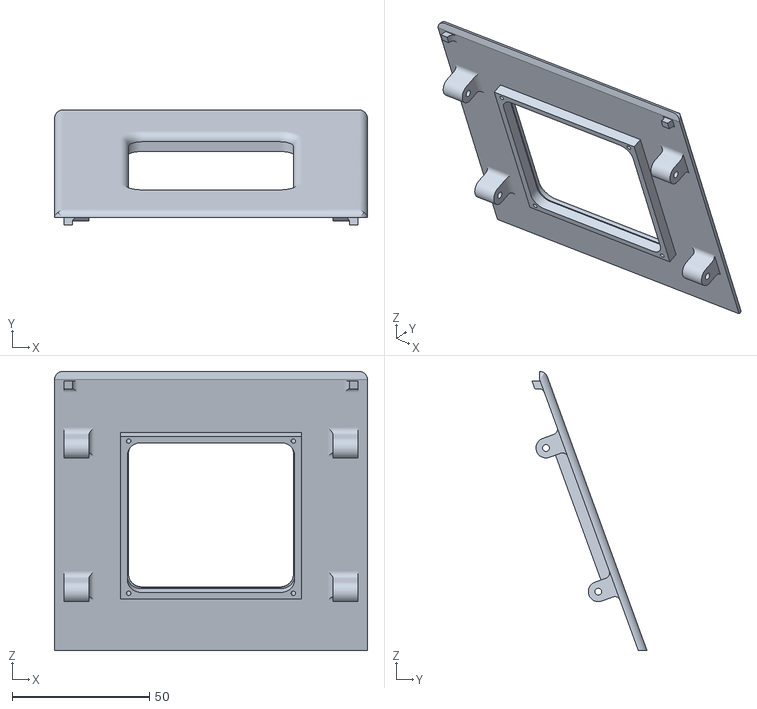
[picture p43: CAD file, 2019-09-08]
Fichiers STL/Panneau Clavier.stl
114.0 x 41.9 x 101.7

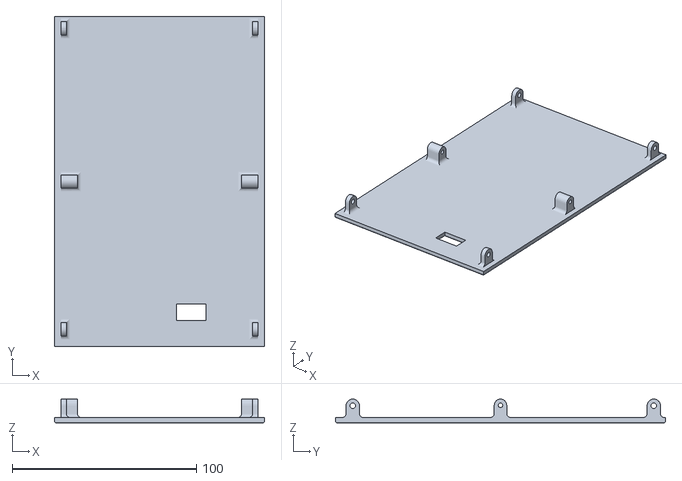
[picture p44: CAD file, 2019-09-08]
Fichiers STL/Panneau Arrière.stl
114.0 x 179.0 x 13.0

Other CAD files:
Fichiers STL/réservoir 2 euros.stl
Fichiers STL/Platine Droite.stl
Fichiers STL/réservoir 10 centimes.stl
Fichiers STL/Patte arrière courte.stl
3D model/Bielle v2 v2.f3d
3D model/Fond sans support CàP.f3d
3D model/Panneau Arrière.f3d
3D model/Panneau Clavier.f3d
3D model/Panneau Ecran.f3d
3D model/Panneau Supérieur.f3d
3D model/Panneau frontal avec support CàP.f3d
3D model/Panneau latéral droit.f3d
3D model/Panneau latéral ouvert.f3d
3D model/Panneau rail 2.f3d
3D model/Panneau rail 3.f3d
3D model/Panneau rail.f3d
3D model/Pivot Clips v2 v4.f3d
3D model/Platine Droite Connecteur carte à puce.f3d
3D model/Platine Gauche Connecteur carte à puce.f3d
3D model/Poussoir v1.f3d
3D model/Tiroir.f3d
3D model/réservoir 1 euro (1).f3d
3D model/réservoir 1 euro (2).f3d
3D model/réservoir 1 euro.f3d
Fichiers STL/Fond.stl
Fichiers STL/Panneau Ecran.stl
Fichiers STL/Panneau Supérieur.stl
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

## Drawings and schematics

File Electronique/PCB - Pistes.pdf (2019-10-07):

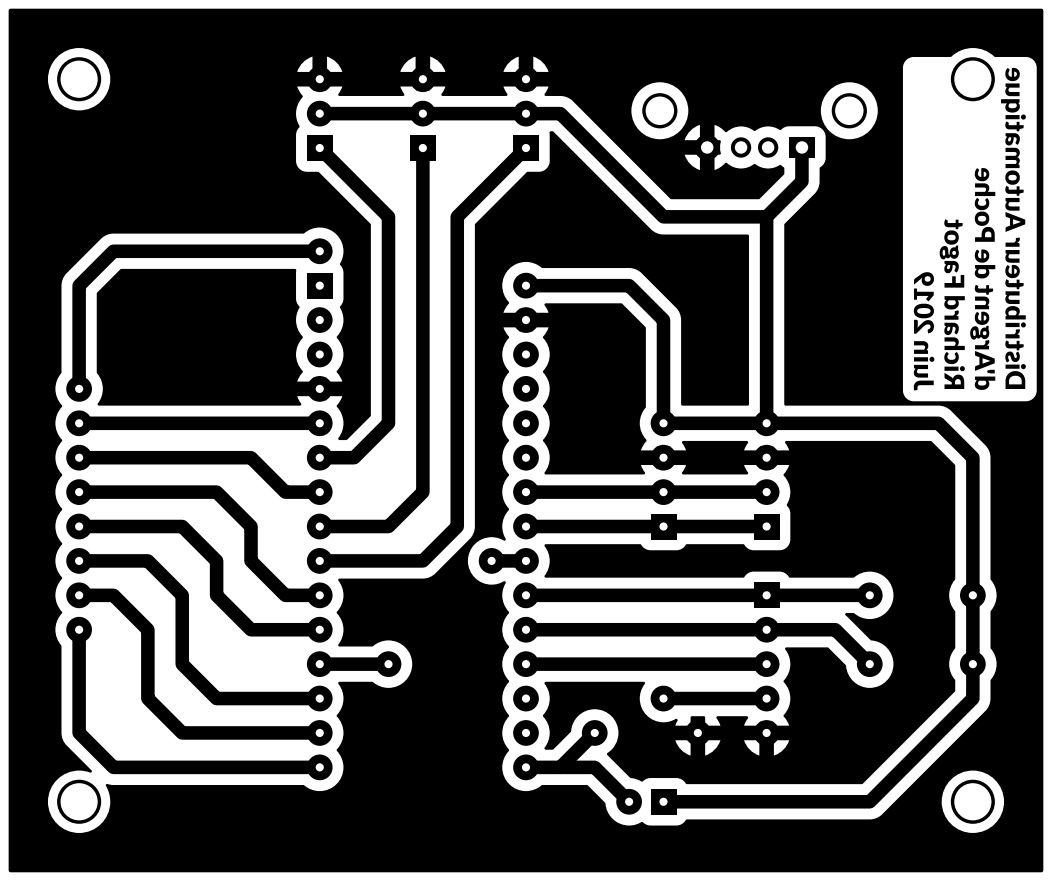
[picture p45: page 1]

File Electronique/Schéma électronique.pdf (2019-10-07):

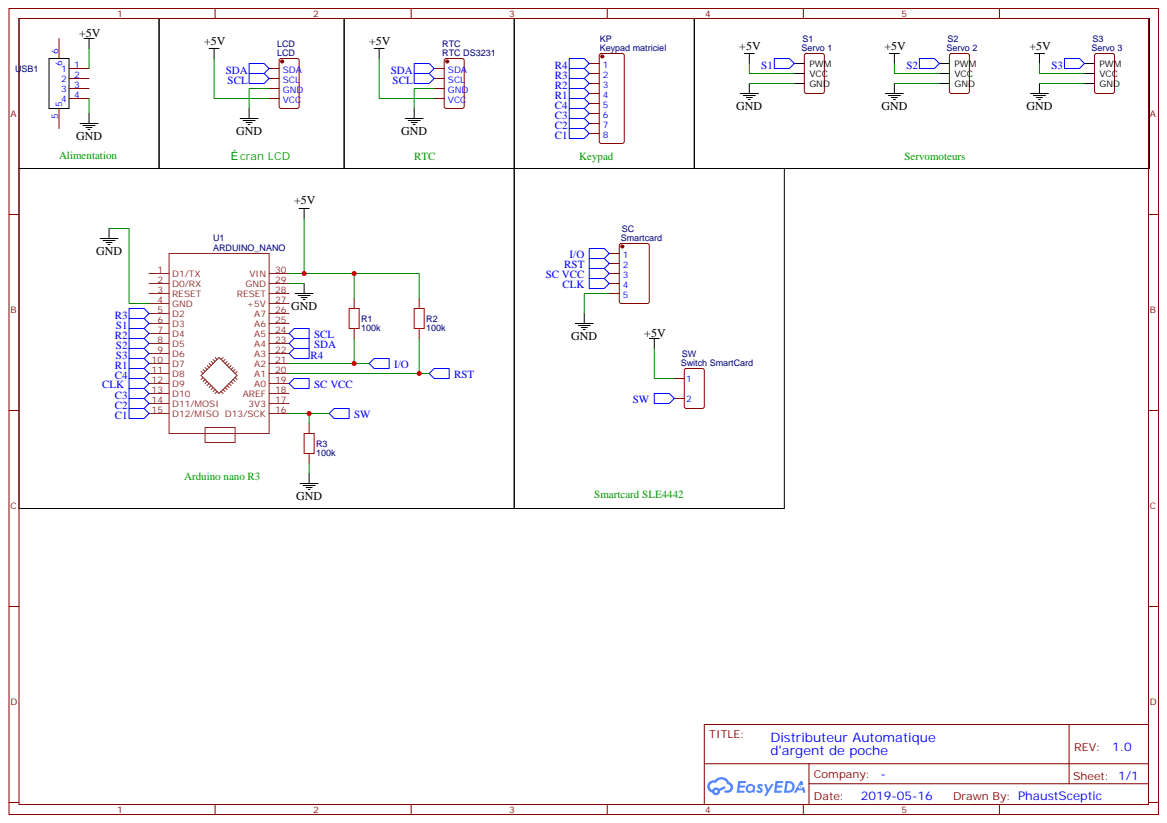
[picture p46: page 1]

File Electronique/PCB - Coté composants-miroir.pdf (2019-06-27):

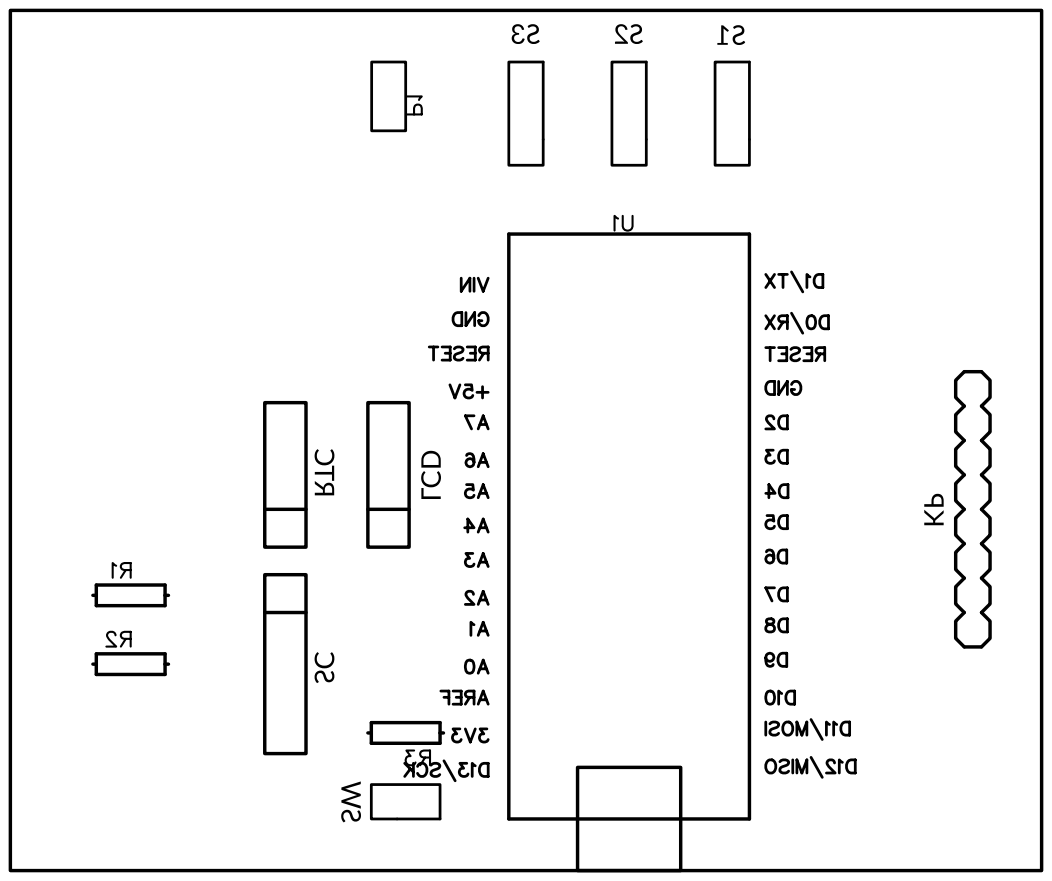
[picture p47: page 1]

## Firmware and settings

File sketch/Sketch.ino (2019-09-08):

//#define DAAP_DEBUG 1

#include <Servo.h>  // Librairie par défaut
#include <string.h>
#include "PocketMoneyDistributor.h"
#include "Displayer.h"
#include "StateMachineEnum.h"
#include "SmartCard.h"
#include "MyKeypad.h"
#include "MyTime.h"
#include "DistributionAllower.h"
#include "LastDistribution.h"


void printTime(boolean = false);
SmartCard sc;
MyKeypad kp;
PocketMoneyDistributor distributor;
Displayer displayer;
MyTime time;
DistributionAllower allower;
///////////////////////////////////////////////////////////////////////////////
//
// États de l'automate fini.
//
///////////////////////////////////////////////////////////////////////////////
state STATE;
state nextState;
unsigned long delayInterval;
unsigned long previousMillis;



static const int BASE = 10; // Le code tapé au clavier est en base 10.
unsigned int userTypedCode = 0; // variable contenant le code saisi par l'utilisateur.

void(* resetFunc) (void) = 0;//declare reset function at address 0

///////////////////////////////////////////////////////////////////////////////
///////////////////////////////////////////////////////////////////////////////
/////////////////////////////** PROGRAMME ** //////////////////////////////////
///////////////////////////////////////////////////////////////////////////////
///////////////////////////////////////////////////////////////////////////////

void setup() {
  #ifdef DAAP_DEBUG
  Serial.begin(9600);
  Serial.println("Debug Mode");
  #endif
  
  time.setup();

  displayer.initialize();
  displayer.addLine("Initialisation");
  displayer.addLine("en cours...");

  // Crée un distributeur contenant 3 types de pièces :
  // - des pièces de 2€ dont le servo est relié à la broche 3 ;
  // - des pièces de 1€ dont le servo est relié à la broche 5 ;
  // - des pièces de 0.20€ dont le servo est relié à la broche 6 ;
  distributor.setup(3, 3, 200, 5, 100, 6, 10);
  distributor.initialize();

  STATE = BEGIN;
  
  // Tests unitaires
  //testSuiteDistributionSequence();
}



void loop() {

  #ifdef DAAP_DEBUG
  captureAndProcessUserEntries();
  #endif
  
  switch(STATE) {

    case BEGIN:
      displayer.clear();
      displayer.addEmptyLine();
      displayer.addEmptyLine();
    	displayer.addLine("Insere ta carte");
      printTime(true);
    	STATE = WAIT_FOR_CARD;
    	break;
    
    case WAIT_FOR_CARD:
      printTime();
     	if(sc.cardInserted()) {
          delay(500);
        	STATE = COLLECT_CARD_DATA;
     	}
    	break;
    
    case COLLECT_CARD_DATA:
      sc.collectSmartcardData(); // appel bloquant.
      time.refreshDate();
      if (allower.isAllowed(sc.getName(), time)) {
        STATE = SAY_HELLO;
      }
      else {
        STATE = NOT_THE_GOOD_DAY;
      }

      break;
    
    case SAY_HELLO: 
    {
      displayer.clear();
      displayer.addLine("Bonjour");
      displayer.addLine(sc.getName());
      displayer.addLine("Entre ton code");
      displayer.addLine("____");
      resetCode();
    	STATE = CAPTURE_USER_ENTRIES;
    }
      break;
    
    case NOT_THE_GOOD_DAY:
    {
      displayer.clear();
      displayer.addLine("Retire ta carte.");
      displayer.addLine("Ce n'est pas le bon");
      char msg[21] = "jour ";
      strcat(msg, sc.getName());
      displayer.addLine(msg);
      displayer.addLine("Reviens samedi !");
      //waitForCardRemoveThenGo(BEGIN);
      STATE = WAIT_FOR_CARD_REMOVE;
      nextState = BEGIN;
    }
      break;
    
    case CAPTURE_USER_ENTRIES:
    	captureAndProcessUserEntries();
    	break;
    
    case GOOD_CODE:
      displayer.clear();
      displayer.addLine("Code bon");
      displayer.addLine("Retire ta carte");
      //waitForCardRemoveThenGo(DISPLAY_DISTRIBUTION);
      STATE = WAIT_FOR_CARD_REMOVE;
      nextState = DISPLAY_DISTRIBUTION;
    	break;
    
    case WRONG_CODE:
      displayer.clear();
    	displayer.addLine("Code Faux");
      //waitThenGo(5000, SAY_HELLO);
      delayInterval = 3000;
      nextState = SAY_HELLO;
      STATE = WAIT;
      previousMillis = millis();
    	break;
    
    case WAIT_FOR_CARD_REMOVE:
    	if(!sc.cardInserted()) {
        sc.cardRemoved();
        STATE = nextState;
    	}
    	break;

    case DISPLAY_DISTRIBUTION:
    {
      displayer.clear();
      displayer.addLine("Distribution de");
      unsigned int pocketMoney = sc.getPocketMoney();

      char totalToDistribute = pocketMoney / 100;
      byte cents = (pocketMoney - totalToDistribute * 100) / 10;
      char msg[21] = {(char)('0' + totalToDistribute), ',', (char)('0' + cents), '0', '\0'};
      strcat(msg, " euro(s)");
      displayer.addLine(msg);

      LastDistribution ld;
      ld.save(sc.getName(), time.getDay(), time.getMonth());

      delayInterval = 1500;
      nextState = DISTRIBUTION;;
      STATE = WAIT;
      previousMillis = millis();
    }
      break;
    
    case DISTRIBUTION:
    {
      distributor.distribute(sc.getPocketMoney());
      if(distributor.hasFinished()) {
        STATE = SAY_GOODBYE;  
      }
    }
    	break;
    
    case SAY_GOODBYE:
      displayer.clear();
      displayer.addLine("Au revoir");
      displayer.addLine(sc.getName());
      //waitThenGo(2000, BEGIN);
      delayInterval = 2000;
      nextState = BEGIN;
      STATE = WAIT;
      previousMillis = millis();
      break;

    case WAIT:
      if(millis() - previousMillis > delayInterval) {
        STATE = nextState;
      }
      break;

    case UNEXPECTED_CARD_REMOVE:
      displayer.clear();
      displayer.addLine("Au revoir");
      //waitThenGo(2000, BEGIN);
      delayInterval = 2000;
      nextState = BEGIN;
      STATE = WAIT;
      previousMillis = millis();
      break;

    default: break;
  }

}

uint8_t previousMinute = 100;

void printTime(boolean force) {
  time.refreshDate();
  if(force || (time.getMinute() != previousMinute)) {
    char timeString[21];
    time.getStringTime(timeString);
    displayer.print(0, timeString);
    previousMinute = time.getMinute();
  }
}



void waitForCardRemoveThenGo(state stateToGOAfterCardRemoved); // nécessaire car le compilateur réorganise l'ordre de déclaration 
                                                              // de telle sorte que la déclaration de la fonction se retrouve
                                                              // avant la déclaration de l'enum.
void waitForCardRemoveThenGo(state stateToGOAfterCardRemoved) {
  STATE = WAIT_FOR_CARD_REMOVE;
  nextState = stateToGOAfterCardRemoved;
}

void waitThenGo(unsigned long interval, state stateToGOAfterWait);
void waitThenGo(unsigned long interval, state stateToGOAfterWait) {
    delayInterval = interval;
    nextState = stateToGOAfterWait;
    STATE = WAIT;
    previousMillis = millis();
}


char star[5] = "____";// chaîne de caractère représentant à l'écran l'endroit ou vont apparaître les étoiles à chaque saisie d'une touche pour le code.
byte keyCount = 0;
/**
 * Capture les entrées saisies au clavier numérique 
 * et lance les actions correspondantes.
 */
void captureAndProcessUserEntries() {

  char customKey = kp.getKey();
  
  if (customKey){
    if(customKey >= 48 && customKey <= 57 && keyCount < 4) { // Saisie du code.
      userTypedCode = userTypedCode * BASE + (customKey - 48);
      star[keyCount] = '*';
      keyCount++;
      
      if(STATE == CAPTURE_USER_ENTRIES) displayer.print(3, star);// on affiche unniquement lorsqu'on est en train de faire la saisie du code.
    }
    
    if(customKey == 'D') { //Validation du code.
      if(sc.checkCode(userTypedCode)) {
        STATE = GOOD_CODE;
      } else {
        STATE = WRONG_CODE;
      }
    }  

    if(customKey == 'B') {
      resetFunc();
    }
    
    if(customKey == 'C') {
      STATE = SAY_HELLO;    
    }

    #ifdef DAAP_DEBUG
    if(customKey == 'A') {
      LastDistribution ld;
      switch(userTypedCode) {
        case 1:
          ld.showEEPROMContent();
          break;
       case 2:
          ld.eraseEEPROMContent();
          break;
      }
      userTypedCode=0;
    }
    #endif
  }
  
}

void resetCode() {
  userTypedCode = 0;
  keyCount = 0;
  strcpy(star, "____");
}

/*****************************************************************************/
/******************************* UNIT TESTS **********************************/
/****************************************************************************
void testSuiteDistributionSequence() {
  // Test exactly one coin, corresponding to the first in the coint list
  byte expectedResult1[] = {0, NO_COIN, NO_COIN, NO_COIN, NO_COIN};
  testDistributionSequence(200, expectedResult1, "Test exactly one coin, corresponding to the first in the coint list");
  
  // Test exactly one coin, corresponding to one not the first in the coint list
  byte expectedResult2[] = {1, NO_COIN, NO_COIN, NO_COIN, NO_COIN};
  testDistributionSequence(100, expectedResult2, "Test exactly one coin, corresponding to one not the first in the coint list");
  
  // Test coin combination
  byte expectedResult3[] = {0, 0, 1, NO_COIN, NO_COIN};
  testDistributionSequence(500, expectedResult3, "Test coin combination");
  
  // Test no combination available (because no corresponding coin found)
  byte expectedResult4[] = {NO_COIN, NO_COIN, NO_COIN, NO_COIN, NO_COIN};
  testDistributionSequence(637, expectedResult4, "Test no combination available (because no corresponding coin found)");
  
  // Test out of bound sequence
  byte expectedResult5[] = {NO_COIN, NO_COIN, NO_COIN, NO_COIN, NO_COIN};
  testDistributionSequence(2200, expectedResult5, "Test out of bound sequence");
}

void testDistributionSequence(int moneyAmount, byte expectedResult[], String title) {
  distributionSequence(moneyAmount);
  
  boolean success = true;
  
  for(byte i  = 0 ; i < MAX_SEQUENCE_STEPS ; i++) {
    if(servoIndexSequence[i] != expectedResult[i]) {
      success = false;
      break;
    }
  }
  
  if(!success) {
    Serial.print("FAIL - "); Serial.println(title);
    Serial.print("Expected - "); printArray(expectedResult, MAX_SEQUENCE_STEPS); Serial.println();
    Serial.print("Was      - "); printArray(servoIndexSequence, MAX_SEQUENCE_STEPS); Serial.println();
  } else {
    Serial.print("SUCCESS - "); Serial.println(title);
  }
  
}
       
 void printArray(byte array[], int size) {
   Serial.print("[");
   for(int i = 0 ; i < size-1; i++) {
     Serial.print(array[i]);
     Serial.print(", ");
   }
   Serial.print(array[size-1]);
   Serial.print("]");
 }
*/

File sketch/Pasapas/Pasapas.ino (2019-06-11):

#include <Keypad.h> //Keypad by Mark Stanley, Alexander Brevig Version 3.1.1
#include <LiquidCrystal_PCF8574.h> // by Mathias Hertel
#include <ds3231.h> //ds3231FS by Petre Rodan
#include <Servo.h>
#include "SL44x2.h" //https://sourceforge.net/p/arduinosclib/wiki/Home/

LiquidCrystal_PCF8574 lcd = LiquidCrystal_PCF8574(0x27);


const uint8_t SC_C2_RST = A1;
const uint8_t SC_C1_VCC = A0;
const uint8_t SC_C7_IO = A2;
const uint8_t SC_C2_CLK = 9;
const uint8_t SC_SWITCH_CARD_PRESENT= 13;
const boolean SC_SWITCH_CARD_PRESENT_INVERT = false;
SL44x2 sl44x2(SC_C7_IO, SC_C2_RST, SC_C1_VCC, SC_SWITCH_CARD_PRESENT, SC_C2_CLK, SC_SWITCH_CARD_PRESENT_INVERT);

const byte ROWS = 4; 
const byte COLS = 4; 

char hexaKeys[ROWS][COLS] = {
  {'1', '2', '3', 'A'},
  {'4', '5', '6', 'B'},
  {'7', '8', '9', 'C'},
  {'*', '0', '#', 'D'}};
  
byte rowPins[ROWS] = {7, 4, 2, A3}; 
byte colPins[COLS] = {12, 11, 10, 8};  

Keypad customKeypad = Keypad(makeKeymap(hexaKeys), rowPins, colPins, ROWS, COLS); 


static const byte BASE = 10; // Le code tapé au clavier est en base 10.
unsigned int userTypedCode = 0; // variable contenant le code saisi par l'utilisateur.
byte index = 7;


Servo s1, s2, s3;

const byte s1_pin = 3;
const byte s2_pin = 5;
const byte s3_pin = 6;

void setup() {
  // put your setup code here, to run once:
  Serial.begin(9600);

  lcd.begin(20, 4);
  lcd.setBacklight(255);
  clrscr();


  DS3231_init(DS3231_INTCN); //register the ds3231 (DS3231_INTCN is the default address of ds3231, this is set by macro for no performance loss)

  moveServos(180);
}

enum codeState {
  INSERT_CARD,
  WAITING_CARD,
  READ_DATA,
  INVITE_CODE,
  GOOD,
  BAD,
  WAIT_REMOVE,
  DISTRIB,
  WRITING
};

codeState codeResult = INSERT_CARD;
int secretCode = 0;
int money = 0;
char name[21] = "";

void loop() {
  captureAndProcessUserEntries();
  displayTime();
  switch(codeResult) {
    case INSERT_CARD:
      clrscr();
      lcd.setCursor(0, 2);
      lcd.print("  INSERER LA CARTE  ");
      printTime();
      codeResult = WAITING_CARD;
      break;
    case WAITING_CARD:
      if(sl44x2.cardInserted()) {
        codeResult = READ_DATA;
      }
      break;
    case READ_DATA:
      if (sl44x2.cardReady()) {
        uint8_t  data[1+4+3+20];
        uint16_t i = sl44x2.readMainMemory(0x60, data, 28);
        if (i > 0) {
          sl44x2.dumpHEX(data, i);
        }
        int length = data[0];
        secretCode = toInt(data[1])*1000 + toInt(data[2])*100 + toInt(data[3])*10 + toInt(data[4]);
        money = toInt(data[5])*100 + toInt(data[6])*10 + toInt(data[7]);
        strncpy(name, data+8, length);
        name[length] = '\0';
        codeResult = INVITE_CODE;
      }
      break;
    case INVITE_CODE:
      clrscr();
      lcd.print("CODE : ");
      lcd.setCursor(0, 3);
      lcd.print(name);
      printTime();
      codeResult = WRITING;
      break;
    case GOOD:
      clrscr();
      lcd.print("CODE BON");
      lcd.setCursor(0, 1);
      lcd.print("RETIRE LA CARTE");
      printTime();
      delay(2000);
      codeResult = WAIT_REMOVE;
      userTypedCode = 0;
      break;
    case WAIT_REMOVE:
      if(!sl44x2.cardInserted()) {
        sl44x2.cardRemoved();
        codeResult = DISTRIB;  
      }
      break;
    case DISTRIB:
      distribute();
      codeResult = INVITE_CODE;
      break;
    case BAD:
      clrscr();
      lcd.print("CODE FAUX");
      printTime();
      delay(2000);
      codeResult = INVITE_CODE;
      userTypedCode = 0;
      break;
    default:
      break;
  }
}

int toInt(char c) {
  return (int)(c - 48);
}
void moveServos(byte direction) {
  s1.attach(s1_pin);
  s1.write(direction);
  s2.attach(s2_pin);
  s2.write(direction);
  s3.attach(s3_pin);
  s3.write(direction);

  delay(2000);
  s1.detach();
  s2.detach();
  s3.detach();  
}

void distribute() {
  moveServos(0);
  moveServos(180);
}

ts timeDetails;
byte minute = 0;
void displayTime() {
  DS3231_get(&timeDetails);
  byte tdMin = (byte)timeDetails.min; 
  if(tdMin != minute) {
    printTime();
  }
    
}

void printTime() {
  DS3231_get(&timeDetails);  
  
  uint8_t tdH = timeDetails.hour;
  byte tdMin = (byte)timeDetails.min;
  
  byte a = tdH / 10 ;
  byte b = tdH - a * 10;
  byte c = tdMin / 10;
  byte d = tdMin - c * 10; 
  char s[6] = {'0' + a, '0' + b, ':', '0' + c, '0' + d, '\0'};

  lcd.setCursor(15,0);
  lcd.print(s);  
}


void clrscr() {
  lcd.setCursor(0, 0);
  lcd.clear();
}

void captureAndProcessUserEntries() {

  char customKey = customKeypad.getKey();
  
  if (customKey){
    if(customKey >= 48 && customKey <= 57) {
      userTypedCode = userTypedCode * BASE + (customKey - 48);
      lcd.setCursor(7, 0);
      lcd.print(userTypedCode);
    }
    
    if(customKey == 'D') {
      if(userTypedCode == secretCode) {
        Serial.println("OK");
        codeResult = GOOD;
      } else {
        Serial.println("KO");
        codeResult = BAD;
      }
    }  

    if(customKey == 'C') {
      userTypedCode = 0;
    }
  }
  
}

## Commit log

2019-05-15 Ajout des listes de matériel et logiciels
2019-05-16 On commence à supprimer les delay
2019-05-20 Encapsulation de la partie distributeur.
2019-05-20 Suppression des String de ::log() et ::display(). on passe de 8466o à 8068o
2019-05-20 Ajustement des pins, correction de l'état DISTRIBUTION, mock du clavier
    [CoinPusher.cpp]
2019-05-21 Gestion de l'écran, RTC, logique applicative
2019-05-22 Mise en place d'un état WAIT et modification de l'état WAIT_FOR_CARD_REMOVE
2019-05-22 Suppression des fonctions ::display() qui n'étaient plus utiisées
2019-05-22 Première optimisation de la taille du programme en remplaçant les string par des char
2019-05-24 Ignore les fichiers temporaire de dia
2019-05-24 Diagramme des étapes du programme
2019-05-24 Homogénéisation des noms des répertoires
2019-05-24 Ajout de la partie électronique
2019-05-28 Ajout de références
2019-05-28 Ajout de la référence vers la lib SLE4442
2019-05-29 Ajout de conseils
2019-05-29 Gérer les parasites
2019-06-02 Préparation de la prez
2019-06-03 Complétion de la présentation
2019-06-05 Conseils sur la création du PCB
2019-06-05 Correction suite ajout d'un servo, mappage des pin identique à easyEDA, suppression des appels de fonction avec un enum en paramètre
    [Sketch.ino]
2019-06-10 Vérification des servos
2019-06-12 Travail sur la présentation
2019-06-12 Nettoyage de code commenté et correction d'erreur de compilation sous VSCode
    [Sketch.ino]
2019-06-12 Extraction dans une classe du code de la carte à puce
2019-06-12 Extraction de la classe MyKeypad
2019-06-12 Cas du débordement de mémoire
2019-06-12 Extraction des pin dans des define
2019-06-12 Ajout des variabtion de la taille du programme
2019-06-13 Affichage heure + code + fix
    [Sketch.ino]
2019-06-13 Forçage de l'affichage de l'heure + permettre à l'utilisateur de corriger son code
    [Sketch.ino]
2019-06-18 Idée pour les évolutions futures
2019-06-20 Abandon de pandoc
2019-06-21 /!\ NE COMPILE PAS !!!!! Ajout de la mécanique d'autorisation de distribution
2019-06-22 Corrections du dernier commit + ajout DEBUG + options de debug
    [DistributionAllower.cpp, LastDistribution.cpp, Sketch.ino]
2019-07-01 Sav élec + discours
    [daap.kicad_pcb, daap.sch]
2019-07-04 Faut prévoir plutôt une demi journée de conf...
    [Clip.f3d, Clip.obj, Clip.stl]
2019-07-09 Il semblerait que cela tienne en 1h
2019-08-11 Doc. conception des platines de support du connecteur de carte à puce
2019-08-13 Vérifier si il faut ajouter du dissolvant sur le papier après son aposition sur le cuivre
2019-09-08 Fichiers STL et peaufinage du code
    [Fond sans support CàP.stl, Panneau Arrière.stl, Panneau Clavier.stl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]
2019-09-16 Ajout de notes
2019-09-23 Génération des fichiers STL
    [Antichutte.stl, Bielle v2.stl, Clip.f3d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]
2019-09-26 Début des corrections suite à la présentation à blanc
2019-10-02 Amélioration des couleurs
2019-10-07 Acualisation des ressources
    [Antichutte.stl, Bielle v2 v2.f3d, Bielle v2.stl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]
